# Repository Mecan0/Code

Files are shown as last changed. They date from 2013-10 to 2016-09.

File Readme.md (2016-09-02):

IMPRESORA 3D POWERCODE
 
LISTA DE MATERIALES
 
MARCO COMPLETO POWERCODE CON PLATAFORMA NIVELABLE 3 PUNTOS (7 PIEZAS)

1-. CAJA TORNILLERÍA Y PEQUEÑO MATERIAL:

1 TORNILLERÍA COMPLETA (Ver despiece), 
2 POLEAS GT2 20 DIENTES, 
2 ACOPLADORES 5X5, 
11 RODAMIENTOS LINEALES LM8UU 2 METÁLICOS Y 9 PLÁSTICOS, 
4 PINZAS PARA CRISTAL, 
2 RODAMIENTOS 685ZZ, 
20 BRIDAS 2.5 X 100, 4 BRIDAS 3.5X150,
2 CORREAS GT2 (850 mm Eje X y 650 mm Eje Y)

2-. PAQUETE PLATAFORMA CALIENTE

PLATAFORMA CALIENTE
1 CRISTAL (Ver plano)
1 LÁMINA DE CORCHO 215 X 215 y trozo.
1 CABLE ROJO-NEGRO, TERMISTOR Y FUNDA TERMORETRÁCTIL.

3-. VARILLAS LISAS Y ROSCADAS

4 VARILLAS LISAS CALIBRADAS  ACERO F114 CROMADO 8 X 380 MM
2 VARILLAS LISAS CALIBRADAS ACERO F114 CROMADO X 330 MM
2 VARILLAS ROSCADAS M10X390
2 VARILLAS ROSCADAS M5X300

4-. SOPORTE ROLLO

2 VARILLAS M8X180, TUBO GEWIS 20X220, 4 TUERCAS M8 Y ARANDELAS PIEZAS PLÁSTICAS.

5-. EXTRUSOR Y FUSOR

EXTRUSOR TITAN + HOTEND E3D LITE V6 Y CABLEADO.

6-. MOTORES:

5 MOTORES PASO A PASO MOTECH, 200 PASOS/REV, 4500 KG· CM, CON CONECTOR Y EJE FRESADO, 40 MM DE LONGITUD. REF: MT1703HS168A  160118.
5 CABLES PARA MOTORES. 

7-. FUENTE DE ALIMENTACIÓN

1 FUENTE DE ALIMENTACIÓN 12v 20A, 

8-. CABLEADO POTENCIA Y CONEXIÓN USB.

1  CABLE ALIMENTACIÓN 230V CON ENCHUFE  SCHUCO 1M,
1 CABLE USB  1.8M, 
1 CABLE ALIMENTACIÓN ELECTRÓNICA 12V, 4x1MM DE 53 CM.
1 INTERUPTOR

9-. ELECTRÓNICA

1 ELECTRÓNICA RAMPS 1.4SB
1 ARDUINO MEGA 2560 R3,
 4 DRIVERS DRV8825 (32 MICROPASOS) con DISIPADORES Y FIRMWARE CARGADO.  

10-. DISPLAY, BLOWER Y FINALES DE CARRERA

1 DISPLAY LCD 20X4
1 VENTILADOR RADIAL 50X50X15 12v (BLOWER) Y 1 CABLE PARA BLOWER 60 CM,
3 FINALES DE CARRERA PCB CON CONECTOR Y CABLE DE 70 CM.

11-.  TORNILLERÍA POWER CODE 3P EXTRUSOR E3D+TITAN

16	Torn 3x10 para plástico	 		Para finales de carrera 9, ventilador 3, Xend 2
12	M3x10	 DIN912		Para motores  2+2+2+3, para fuente 2.
10	M3x16	 DIN912		Para plataforma 4, LCD 4,
5	M3x20	 DIN912		Para ventilador 2
10	M3x25	 DIN912		Para electrónica 3, Para LCD 2,
 		 		
30	Tuercas M3	DIN934		
30	Arandelas M3	DIN125		
 		 		
2	Tornillo M5x25 	DIN933		Para tensores 2
1	Tornillo M5x40	DIN84		Para tensor X
2	Varillas M5x300	 		
 		 		
6	Tuercas M5	DIN934		Para eje Z 2, para tensores 3,
2	Tuercas M5 autoblocantes	DIN985		Para tensores 2
10	Arandelas M5	DIN125		Para tensores 4x2
8	Arandelas M5 vuelo	DIN9021		Para tensores 3x2
 		 		
13	Tornillos Seta M6x20	DIN603		Para Marco 4, para diagonales 8, motor Y 1,
2	Tornillos M6x30	DIN84		Para plataforma abajo 1 y Para tensor Y 1
1	Tornilo de M6x35	DIN933		Para plataforma rótula 1
2	Esparragos M6 	 		Para nivelado plataforma
 		 		
30	Tuercas M6	DIN934		
2	Tuercas M6 autoblocantes	DIN985		Para Plataforma nivelable
20	Arandelas M6	DIN125		
10	Arandelas M6 vuelo	DIN9021		
 		 		
2	Varillas M10x390	 		Eje Y
12	Tuercas M10	DIN934		Para varillas 12
8	Arandelas M10	DIN125		Para varillas 8
4	Arandelas M10 Vuelo	DIN9021		Para varillas con marco 4

Para soporte rollo	 		
 		 		
2	Varillas M8x180	 		
4	Tuercas M8	 		
2	Arandelas M8	 		
1	Tubo Gewis de 20x220mm	 		

Basada en la Prusa I3. Xcarriage basado en el diseño de Girobot, soporte del LCD basado en Prusa Hephestos de BQ.

Licencia creative commons, attribution, share alike.

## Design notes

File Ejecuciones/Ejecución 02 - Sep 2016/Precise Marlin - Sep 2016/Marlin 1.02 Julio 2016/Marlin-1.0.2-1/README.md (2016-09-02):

# Marlin 3D Printer Firmware


 Documentation has moved to [marlinfirmware.org](http://www.marlinfirmware.org).

## Release Branch

The Release branch contains the latest tagged version of Marlin (currently 1.0.2 – January 2015). It also includes a version 1.0.1 (December 2014). Any version of Marlin before 1.0.1 (when we started tagging versions) can be collectively referred to as Marlin 1.0.0.

For the most up-to-date Marlin code, please go to the [Development branch](https://github.com/MarlinFirmware/Marlin/tree/Development) – __Not for production use – use with caution!__ When reporting any issues, please check to see if they are resolved in the Development branch first. But let us know if issues exist in tagged releases so we may document and patch them.

## Current Status: In Development

Marlin development is being accelerated to catch up with a long list of issues. Check the Issues and Pull Requests links on the right to to see what we are currently working on.




##### [RepRap.org Wiki Page](http://reprap.org/wiki/Marlin)

## Contact

__Google Hangout:__ <a href="https://plus.google.com/hangouts/_/gxn3wrea5gdhoo223yimsiforia" target="_blank">. Hangout</a> We have a hangout every 2 weeks. Search the issue list for "Hangout" and you will see what time and date the next event is going on.

## Credits

The current Marlin dev team consists of:

 - Scott Lahteine [@thinkyhead] - English
 - Andreas Hardtung [@AnHardt] - Deutsch, English
 - [@Wurstnase] - Deutsch, English
 - [@fmalpartida] - English, Spanish
 - [@CONSULitAS] - Deutsch, English
 - [@maverikou]
 - Chris Palmer [@nophead]
 - [@paclema]
 - [@epatel]
 - Erik van der Zalm [@ErikZalm]
 - David Braam [@daid]
 - Bernhard Kubicek [@bkubicek]

More features have been added by:
  - Lampmaker,
  - Bradley Feldman,
  - and others...

## License

Marlin is published under the [GPL license](/Documentation/COPYING.md) because We believe in open development.
Do not use this code in products (3D printers, CNC etc) that are closed source or are crippled by a patent.



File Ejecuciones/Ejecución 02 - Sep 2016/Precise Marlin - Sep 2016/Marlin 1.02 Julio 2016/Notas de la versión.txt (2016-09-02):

Basado en Marlin 1.02-1

Cambio el autor de la modificación y la fecha de modificación

Elegir la electrónica:

#define MOTHERBOARD BOARD_RAMPS_13_EFB

Descomentamos la siguiente línea y le damos un nombre:

#define CUSTOM_MENDEL_NAME "PowerCode"

Elegimos los termistores colocados

#define TEMP_SENSOR_0 5
#define TEMP_SENSOR_1 0
#define TEMP_SENSOR_2 0
#define TEMP_SENSOR_BED 1

Limito la temperatura del extrusor principal a 250º

#define HEATER_0_MAXTEMP 250

Seguidamente editamos el PID

// PowerCode con E3D V6 Lite, Thermistor 5, Resistencia 12V a 30W cable azul
// La ultima medició ha sido con en Verano con 30 º

    #define  DEFAULT_Kp 49 //41 // 45.30
    #define  DEFAULT_Ki 7 //5.50 // 6.50
    #define  DEFAULT_Kd 83 //75 // 80.30

Invertimos la dirección del extrusor

#define INVERT_E0_DIR true   // Titan 

Definimos los limites de la impresora

#define X_MAX_POS 195
#define X_MIN_POS 0
#define Y_MAX_POS 190
#define Y_MIN_POS 0
#define Z_MAX_POS 180
#define Z_MIN_POS 0

Colocamos aceleraciones y pasos por mm

//// MOVEMENT SETTINGS
#define NUM_AXIS 4 // The axis order in all axis related arrays is X, Y, Z, E
#define HOMING_FEEDRATE {35*60, 35*60, 2,5*60, 0} //{50*60, 50*60, 4*60, 0}  // set the homing speeds (mm/min)

// default settings

#define DEFAULT_AXIS_STEPS_PER_UNIT   {160.9, 160.9, 8000, 912}  // Driver DRV8825 con 32 micropasos
#define DEFAULT_MAX_FEEDRATE          {200, 200, 2.5, 15} // {500, 500, 5, 25}  // (mm/sec)
#define DEFAULT_MAX_ACCELERATION      {500,500,50,1000} //{9000,9000,100,10000}    // X, Y, Z, E maximum start speed for accelerated moves. E default values are good for Skeinforge 40+, for older versions raise them a lot.

#define DEFAULT_ACCELERATION          500 //3000    // X, Y, Z and E max acceleration in mm/s^2 for printing moves
#define DEFAULT_RETRACT_ACCELERATION  1000 //3000  // X, Y, Z and E max acceleration in mm/s^2 for retracts

Y el Jerk

#define DEFAULT_XYJERK                10.0    // (mm/sec)

Finalmente activamos el LCD

#define REPRAP_DISCOUNT_SMART_CONTROLLER

///////////////////////////////////////////////////////////////////

En la pestaña Language.h elegimos el Español:

#define LANGUAGE_INCLUDE GENERATE_LANGUAGE_INCLUDE(es)

///////////////////////////////////////////////////////////////////

En la ventana configuration_adv, cambiar el retroceso del final de carrera Z a 1

#define Z_HOME_RETRACT_MM 1

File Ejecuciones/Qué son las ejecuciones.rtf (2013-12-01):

¿Qué son las ejecuciones?
Una ejecución es una forma completamente definida de construir la PowerCode, es decir definiendo los rodamientos lineales, el extrusor y hot-end , la electrónica utilizada… todo. De esta forma podremos tener documentación más precisa y completa para cada forma de construir una Code.

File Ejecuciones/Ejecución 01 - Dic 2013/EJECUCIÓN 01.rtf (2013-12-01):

EJECUCIÓN 01

Rodamientos lineales Igus
Electrónica RAMPS
Extrusor tipo Greg Extruder
Hot-end E3D

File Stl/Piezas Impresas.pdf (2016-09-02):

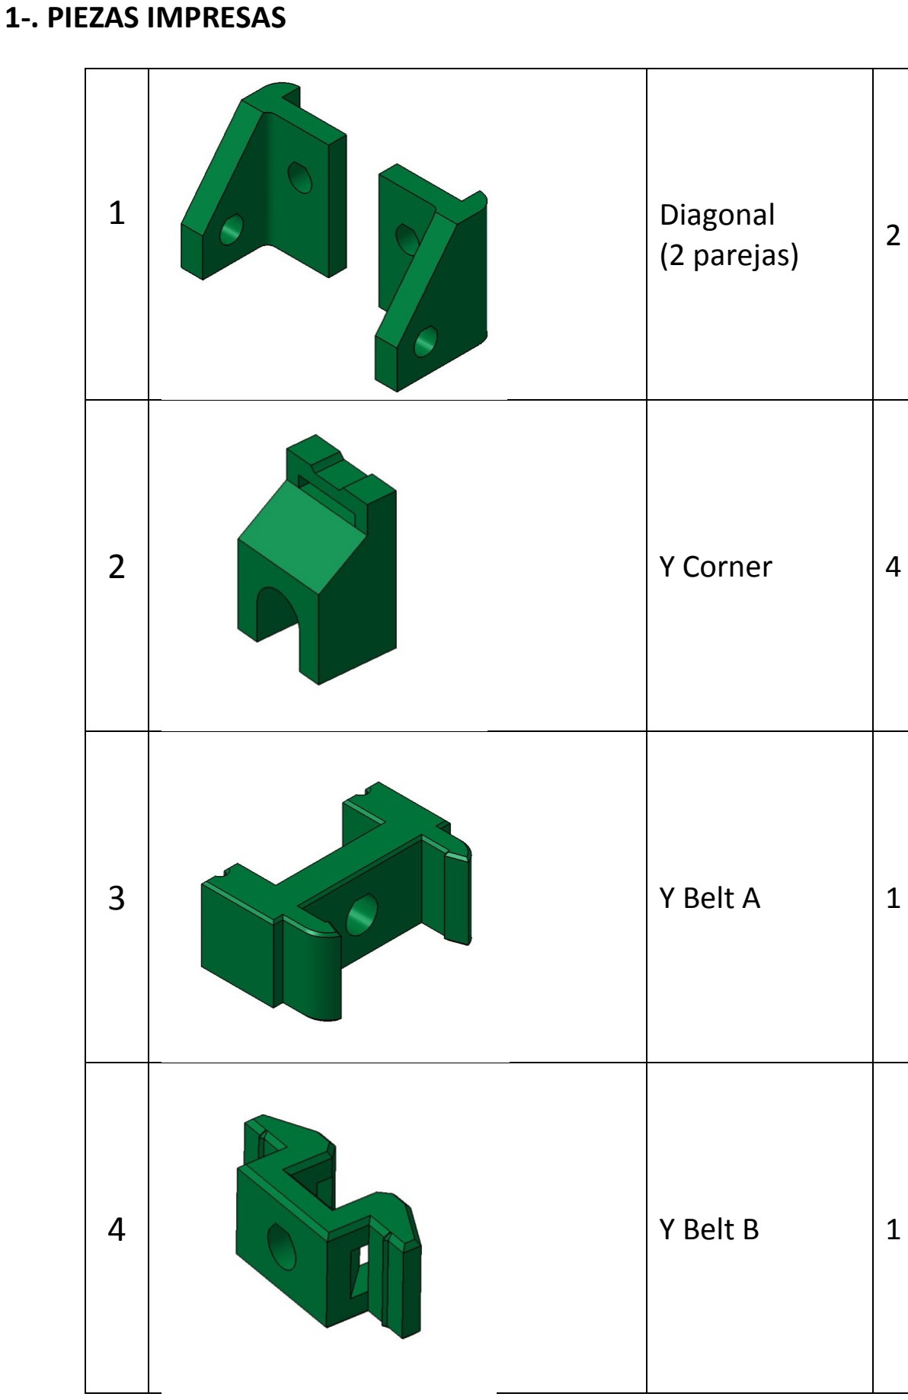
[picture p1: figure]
1-. PIEZAS IMPRESAS; Diagonal (2 parejas); Y Corner; Y Belt A; Y Belt B

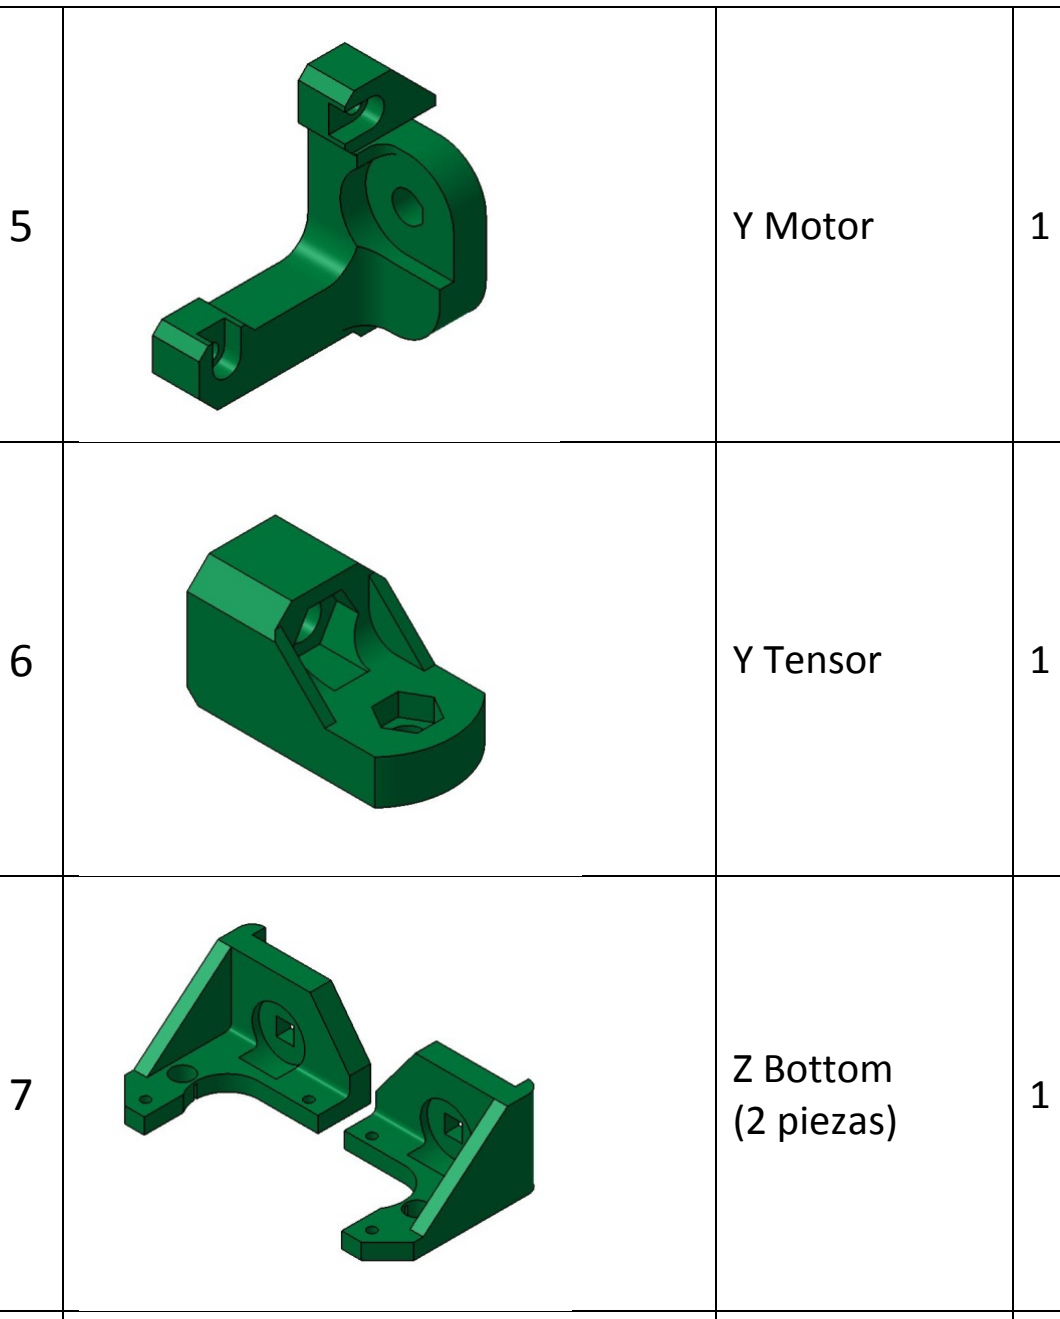
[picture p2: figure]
Y Motor; Y Tensor; Z Bottom (2 piezas)
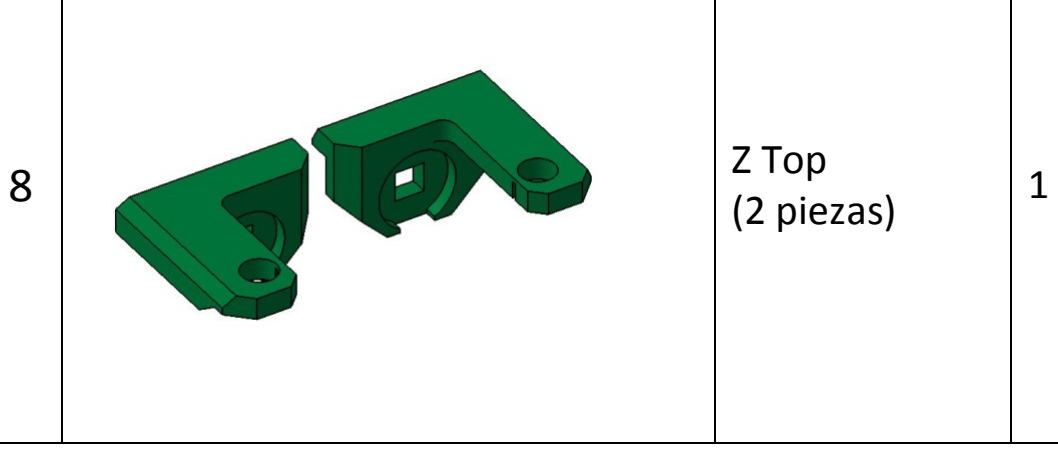
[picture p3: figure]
Z Top (2 piezas)

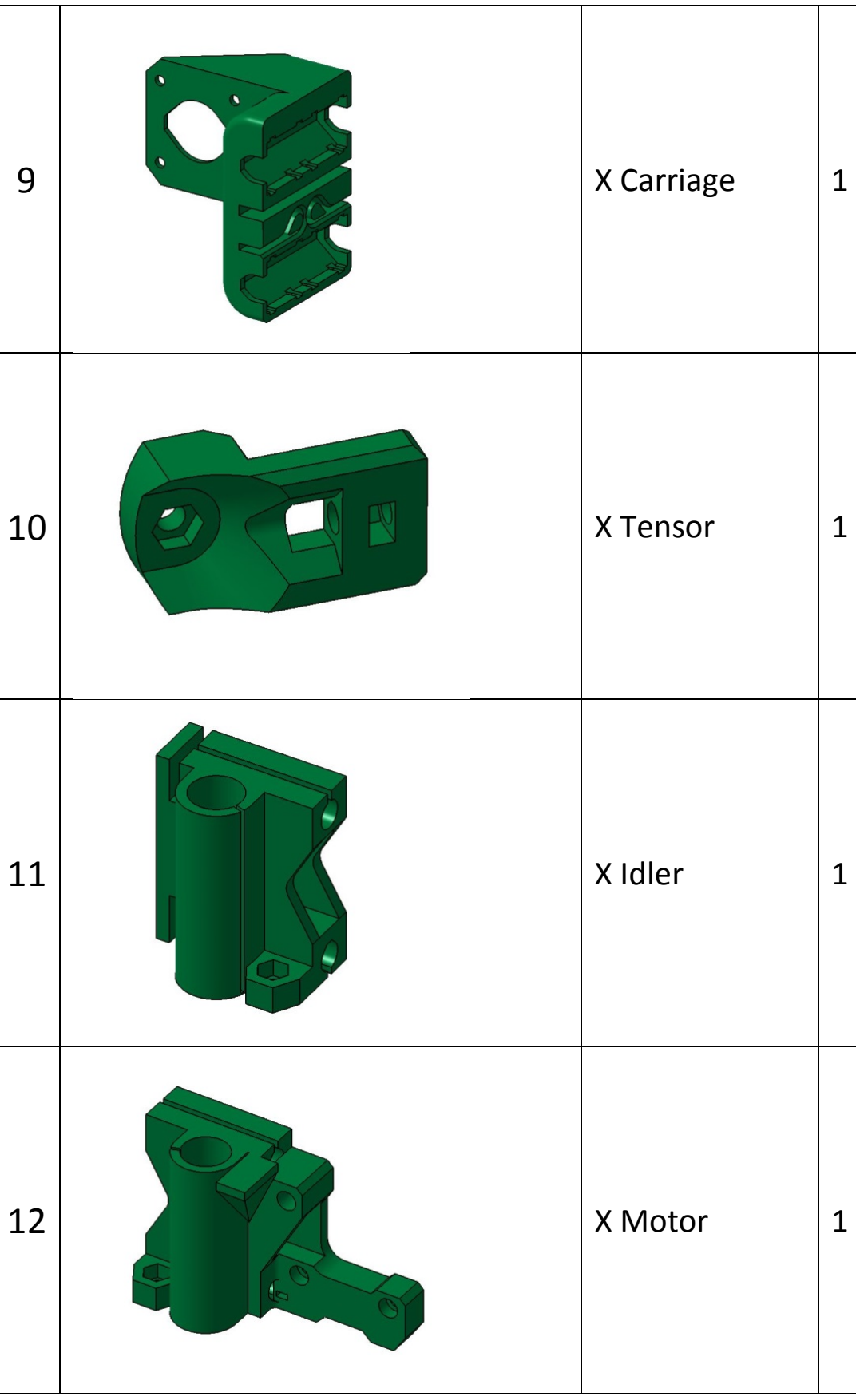
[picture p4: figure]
X Carriage; X Tensor; X Idler; X Motor

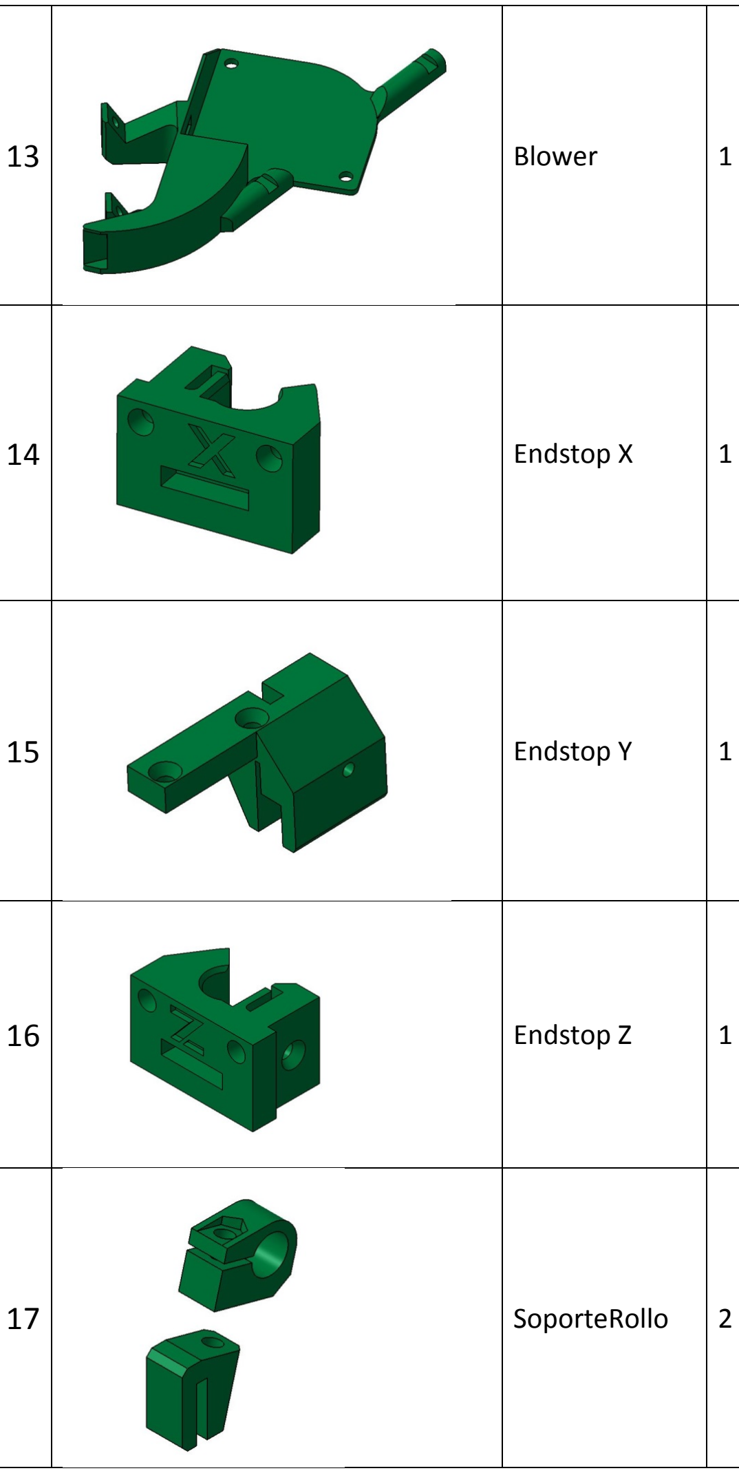
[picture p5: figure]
Blower; Endstop X; Endstop Y; Endstop Z; SoporteRollo

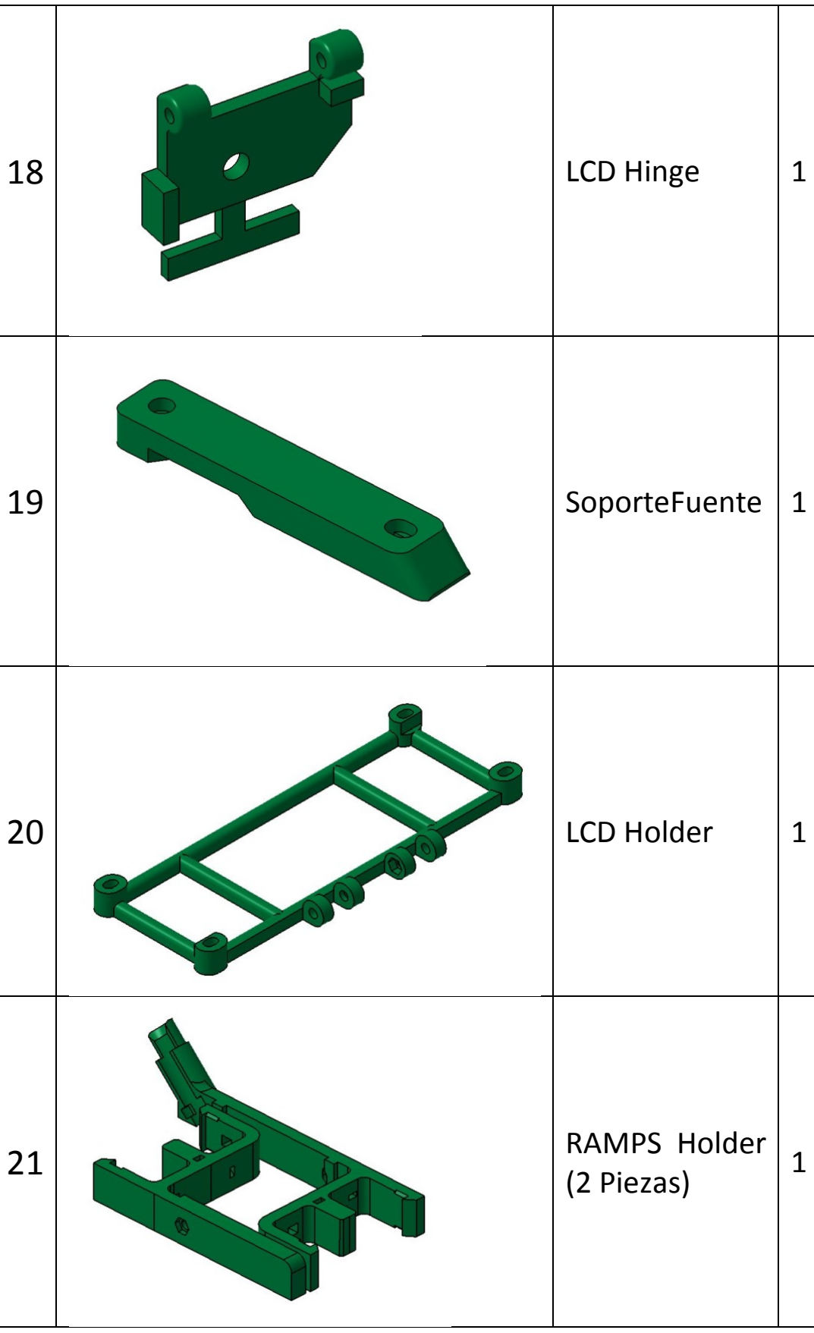
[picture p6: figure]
LCD Hinge; SoporteFuente; LCD Holder; RAMPS Holder (2 Piezas)

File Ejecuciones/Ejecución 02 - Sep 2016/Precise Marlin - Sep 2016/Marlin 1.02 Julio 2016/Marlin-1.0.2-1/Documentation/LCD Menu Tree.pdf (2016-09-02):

# Marlin LCD Menu Tree

Main Menu | Tune Menu | Move Menu
Info screen | Main | Prepare
Tune | Speed | Move 10mm | Move Menu
Prepare | Nozzle | Move 1mm | Move axis
Control | Nozzle2 | Move 0.1mm | Move X
Pause print | Nozzle3 | | Move Y
Resume print | Bed | | Move Z
Stop print | Fan speed | Temperature Menu | Extruder
Print from SD | Flow | Control
Change SD card | Babystep X | Nozzle
No SD card | Babystep Y | Nozzle2
Init. SD card | Babystep Z | Nozzle3
| Change filament | Bed
| | Fan speed
| | Autotemp
| Prepare Menu | \002 Min
| Main | \002 Max | Preheat PLA
| Autostart | \002 Fact | Temperature
| Disable steppers | PID-P | Fan speed
| Auto home | PID-I | Nozzle
| Preheat PLA | PID-D | Bed
| Preheat ABS | PID-C | Store memory
| Cooldown | Preheat PLA conf
| Switch power off | Preheat ABS conf | Preheat ABS
Switch power on | Temperature
Move axis | Fan speed
| Motion Menu | Nozzle
| Control | Bed
Control Menu | Z Offset | Store memory
Main | Accel
Temperature | Vxy-jerk
Motion | Vz-jerk
LCD contrast | Ve-jerk
Retract | Vmax x
Store memory | Vmax y
Load memory | Vmax z
Restore failsafe | Vmax e
| Vmin
| VTrav min
SD Card Menu | Amax x
Main | Amax y
Refresh | Amax z
filenames | Amax e
| A-retract
| Xsteps/mm
| Ysteps/mm
| Zsteps/mm
| Esteps/mm
| Endstop abort

Retract Menu
Control
AutoRetr.
Retract mm
Retract F
Hop mm
UnRet +mm
UnRet F

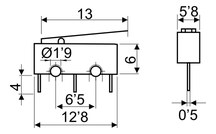
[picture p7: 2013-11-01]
Fuentes/Code Endstop Holder/FinaldeCarrera.png

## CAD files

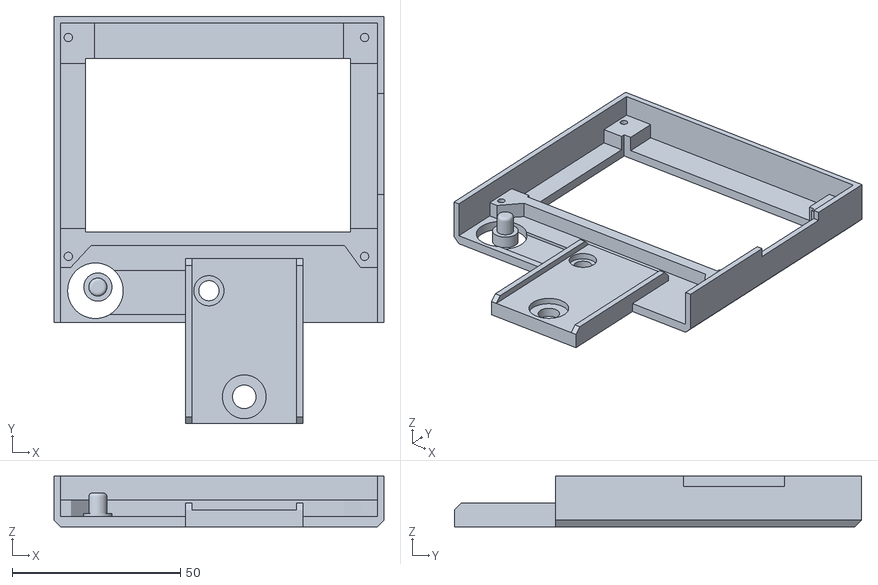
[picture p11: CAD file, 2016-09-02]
Stl/20 LCD FullGraphics.stl
98.0 x 121.0 x 15.0

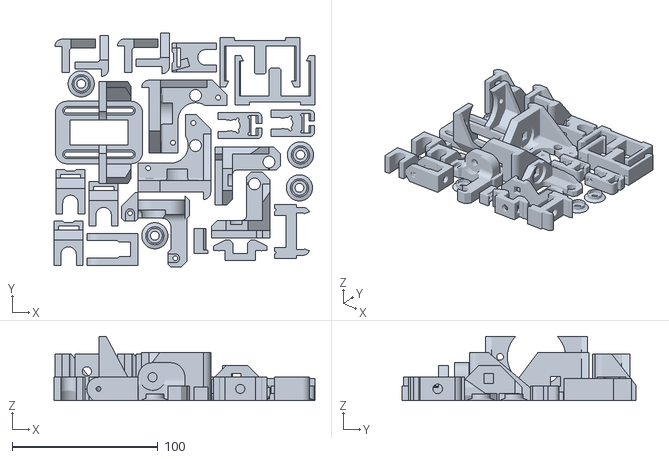
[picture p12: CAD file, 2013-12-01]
Ejecuciones/Ejecución 01 - Dic 2013/Code_Plato_1.stl
179.2 x 160.7 x 44.0

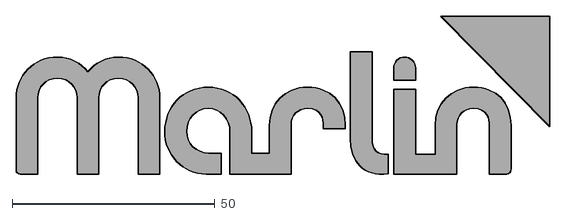
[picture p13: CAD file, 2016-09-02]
Ejecuciones/Ejecución 02 - Sep 2016/Precise Marlin - Sep 2016/Marlin 1.02 Julio 2016/Marlin-1.0.2-1/Documentation/Logo/Marlin Logo.dxf
131.6 x 39.5

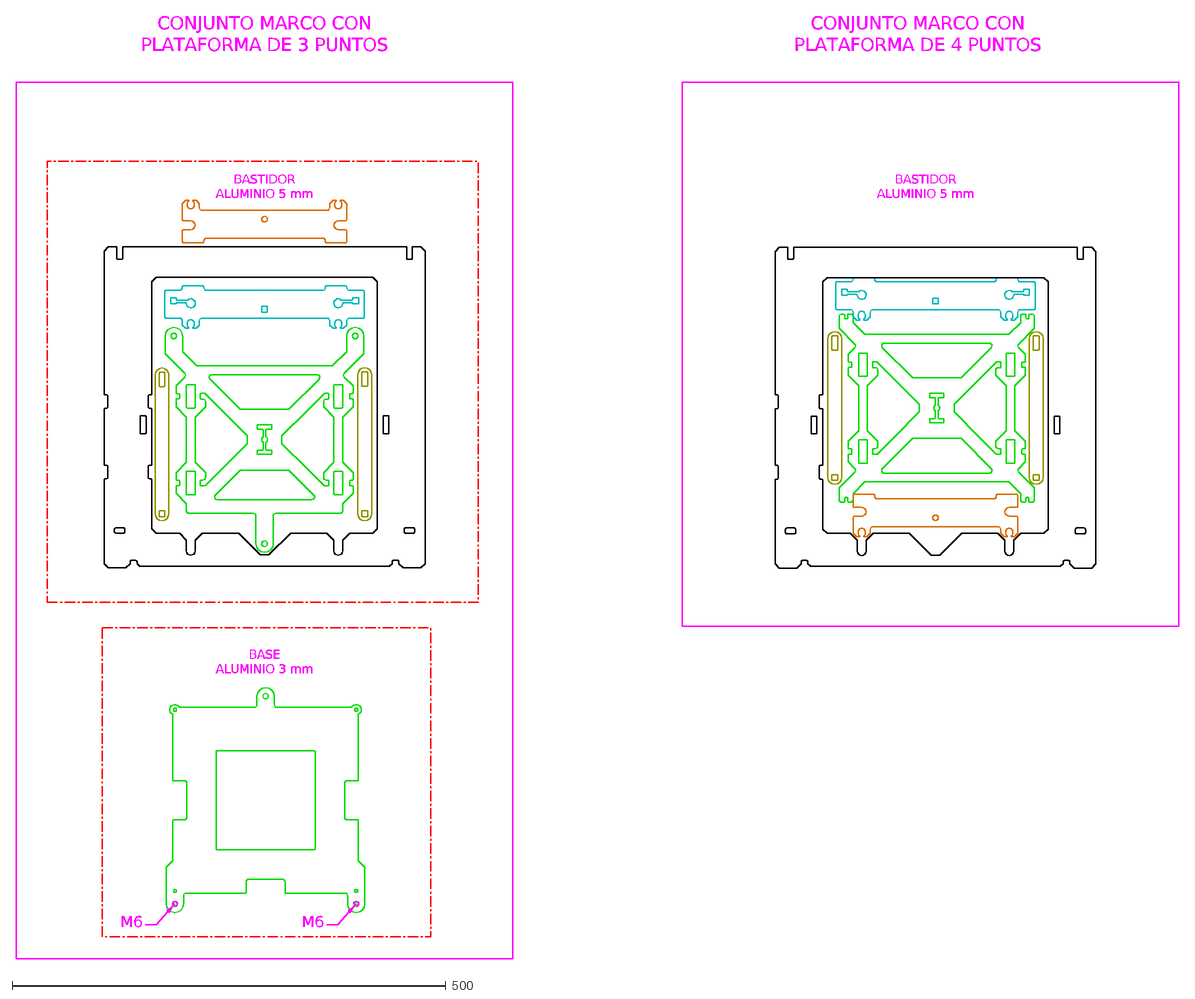
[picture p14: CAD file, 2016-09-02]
Fuentes/Code Aluminio/Aluminio Power Code.dxf
CONJUNTO MARCO CON PLATAFORMA DE 3 PUNTOS
BASE ALUMINIO 3 mm
BASTIDOR ALUMINIO 5 mm
CONJUNTO MARCO CON PLATAFORMA DE 4 PUNTOS
M6

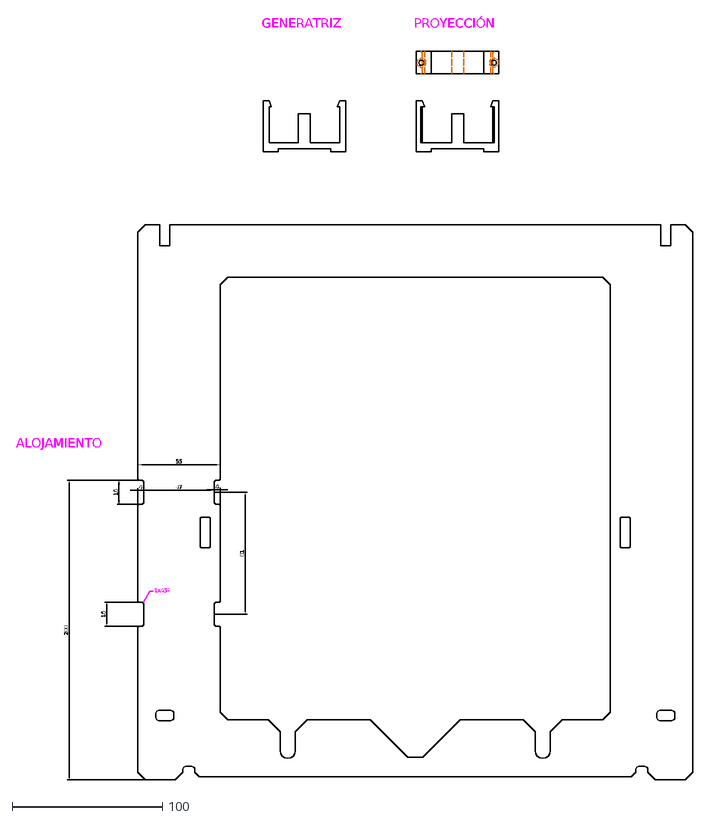
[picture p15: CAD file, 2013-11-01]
Fuentes/Code Clip RAMPS/Code Clip RAMPS.dxf
GENERATRIZ
PROYECCIÓN
16
55
47
4
200
81
1x45º
ALOJAMIENTO

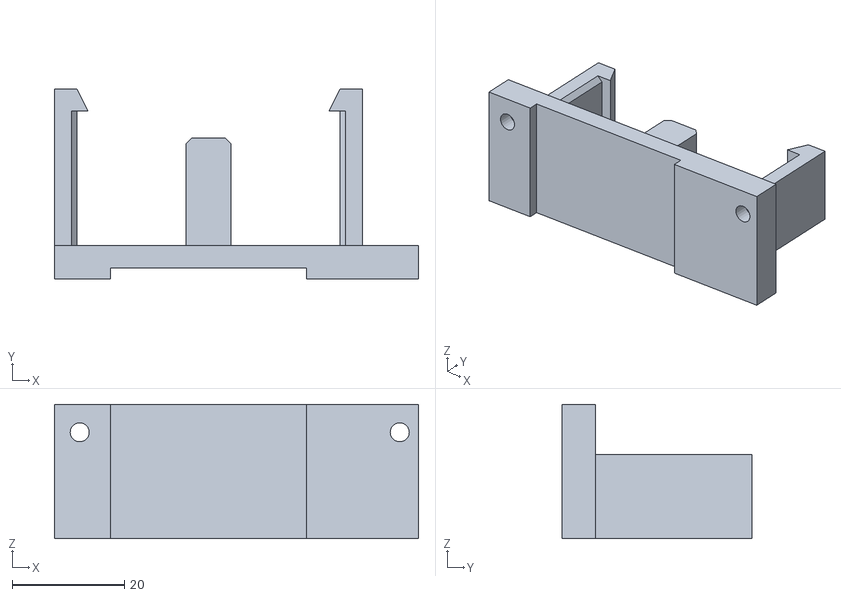
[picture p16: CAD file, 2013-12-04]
Fuentes/Code Clip SAV MK1/Code_Clip_SAV-MK1_arriba.stl
65.0 x 34.0 x 24.0

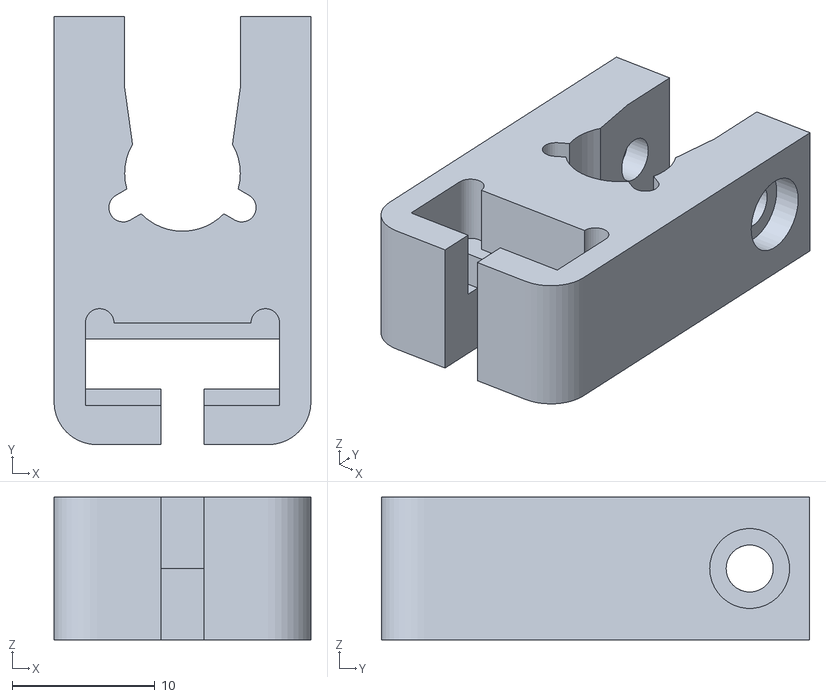
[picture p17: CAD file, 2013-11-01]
Fuentes/Code Endstop Holder/Code_EndStop (x2).stl
18.0 x 30.0 x 10.0

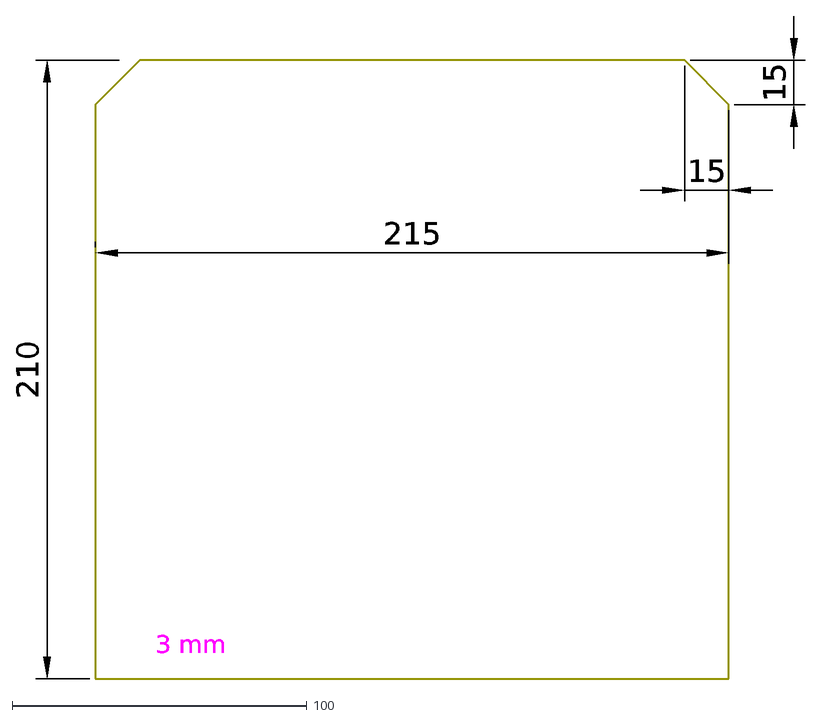
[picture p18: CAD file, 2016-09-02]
Fuentes/Cristal.dxf
215
210
15
3 mm

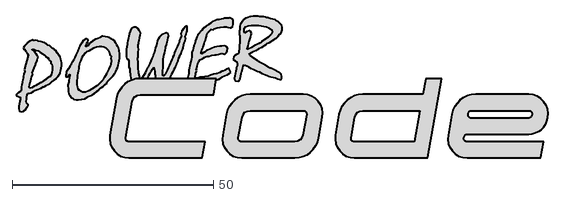
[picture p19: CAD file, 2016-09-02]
Logos/LogoPowerCode.dxf
132.3 x 35.2

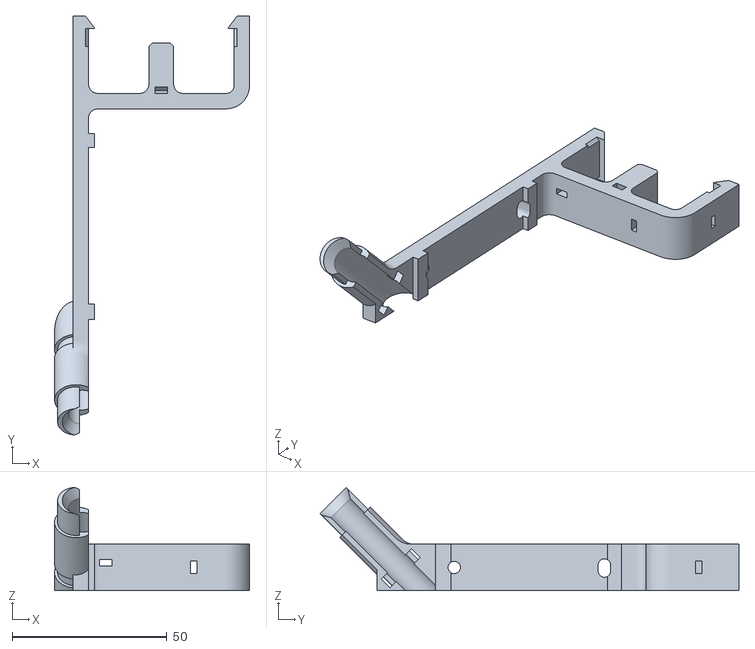
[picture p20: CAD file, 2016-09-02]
Stl/21 RampsHolder Abajo.stl
63.0 x 135.4 x 33.4

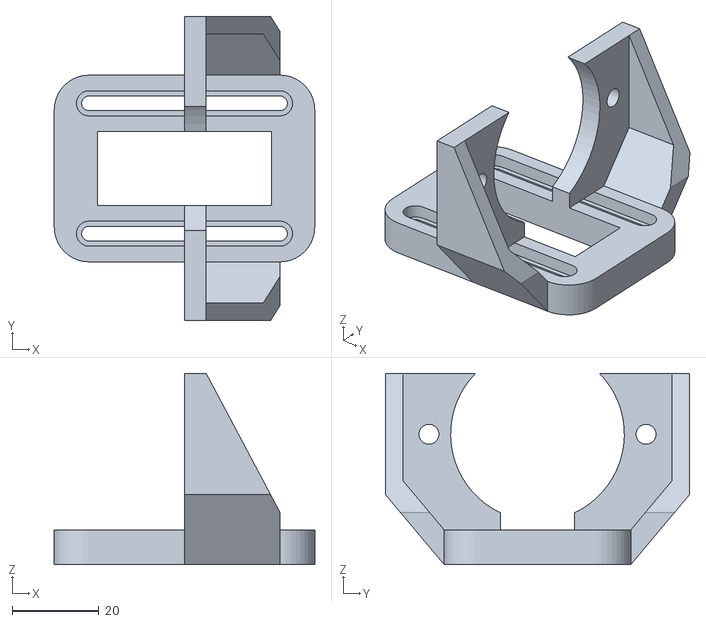
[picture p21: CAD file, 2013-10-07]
Stl/Extruder/Code_LevelExtruder.stl
60.0 x 70.0 x 44.0

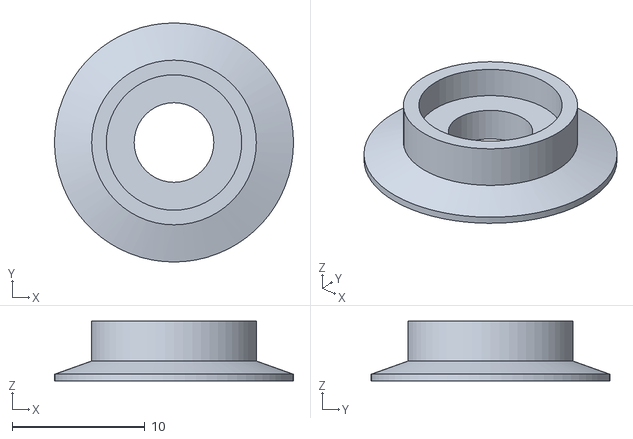
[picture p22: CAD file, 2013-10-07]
Stl/Opcionales-Experimentales/Code_Pulley_623 (x4) diam 10.2.stl
18.0 x 18.0 x 4.50

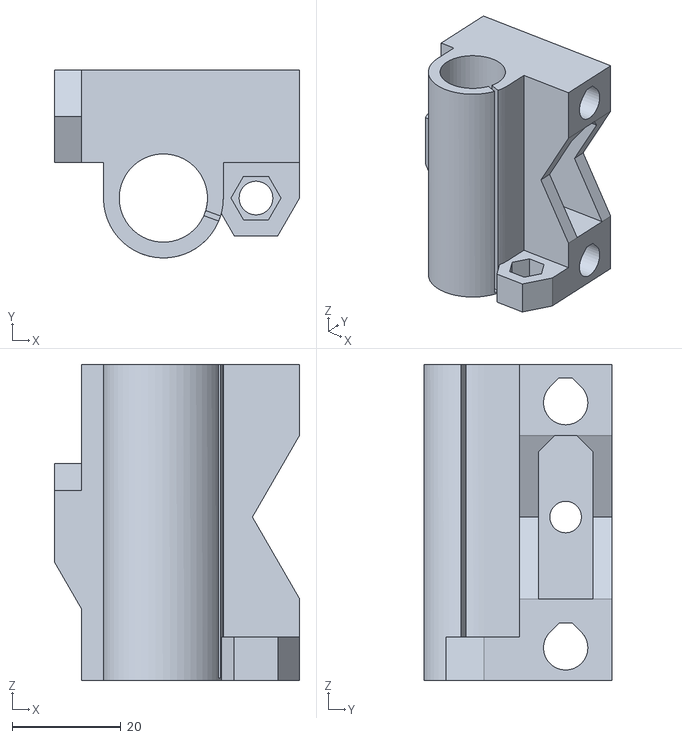
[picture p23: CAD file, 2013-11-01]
Stl/Para Igus/Code_Xend_Idler_A_Igus.stl
45.0 x 34.5 x 58.0

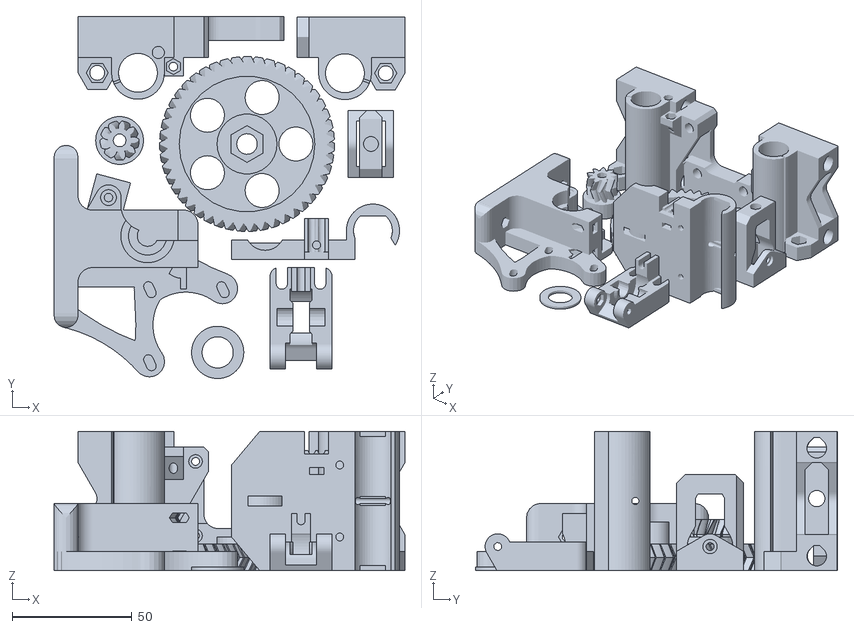
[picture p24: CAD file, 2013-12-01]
Ejecuciones/Ejecución 01 - Dic 2013/Code_Plato_2.stl
146.3 x 151.0 x 58.0

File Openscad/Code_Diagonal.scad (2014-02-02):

// Created from Code_Diagonal (x2).stl
// https://github.com/Mecan0/Code
// By J.Rodigo (www.jra.so)
// Licence Creative commons atribution & share alike.

/**************************/
// Parámetros de la pieza  /
/**************************/

dTalaX = 6.4;	//Diámetro del taladro del bloque X 

dTalaY = 6.4;	//Diámetro del taladro del bloque Y 


// Bloque a lo largo del eje X
module bloqueX(){
	// Bloque y taladro
	difference () {
		translate([0, -6, 0])
		cube([23, 6, 32]);
	
		translate([14.67, 1, 8])
		rotate( 90, [1, 0, 0])
		cylinder(h = 8, r = dTalaX/2, $fn=100);
	}

	// Esquina redondeada
	difference () {
		translate([0, -5, 0])
		cylinder(h = 32, r = 5, $fn=100);

		translate([-5, -10, -1])
		cube([10, 5, 34]);
	}	
}

// Bloque a lo largo del eje Y
module bloqueY(){
	// Bloque y taladro
	difference () {
		translate([0, -23, 0])
		cube([5, 23, 32]);

		translate([-1, -14.66, 20])
		rotate( 90, [0, 1, 0])
		cylinder(h = 7, r = dTalaY/2, $fn=100);
	}
}

// Redondeo entre los bloques X y Y
module redondeoXY(){
	difference () {
		cube([2, 2, 32]);
		
		translate([2, 0, -1])
		cylinder(h = 34, r = 2, $fn=100);
	}
}

// Unión de todos los bloques
module pieza(){
	difference () {
		union() {
			bloqueX();

			bloqueY();

			translate([5, -8, 0])
			redondeoXY();
		}	

		//Chaflan que afecta al bloqueX() y al redondeoXY()
		translate([23, -7, 10.55])
		rotate( 38, [0, -1, 0])
		cube([18, 8, 34]);	
	}
}

/**************************/
//  Generamos las piezas   /
/**************************/

// Pieza normal
translate([0, 30, 0])
pieza();

// Pieza simetrica
translate([0, -30, 0])
mirror([ 0, 1, 0 ]) 
pieza();

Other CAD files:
Fuentes/Code Clip SAV MK1/Code_Clip_SAV-MK1.stl
Fuentes/Code Endstop Holder/CodeEndStopHolder.dxf
Logos/LogoCodeNegativo.stl
Stl/09 X_Carriage Titan.stl
Openscad/Code_Config.scad
Openscad/Code_Xend_Motor.scad
Openscad/Code_Ymotor.scad
Fuentes/Code Clip SAV MK1/Code Clip SAVMK1.dxf
Logos/LogoCode.stl
Openscad/Code_Clip_RAMPS.scad
Openscad/Code_Diagonal (x2).scad
Openscad/Code_EndStop.scad
Openscad/Code_LevelExtruder.scad
Openscad/Code_Pulley_623.scad
Openscad/Code_Xcarriage_A (Nuevo).scad
Openscad/Code_Xcarriage_B.scad
Openscad/Code_Xend_Idler_A_M6.scad
Openscad/Code_Xend_Idler_B_623_M6.scad
Openscad/Code_Ybelt_holderA.scad
Openscad/Code_Ybelt_holderB.scad
Openscad/Code_Ycorner.scad
Openscad/Code_Ycorner_Endstop.scad
Openscad/Code_Yidler_623.scad
Openscad/Code_Zbotton.scad
Openscad/Code_Ztop.scad
Stl/01 Diagonal.stl
Stl/02 Ycorner.stl
Stl/03 Ybelt_A.stl
Stl/04 Ybelt_B.stl
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

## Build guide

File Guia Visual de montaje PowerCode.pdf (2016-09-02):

Guía visual de montaje.


SEP-2016

MARCO, PIEZAS METÁLICAS

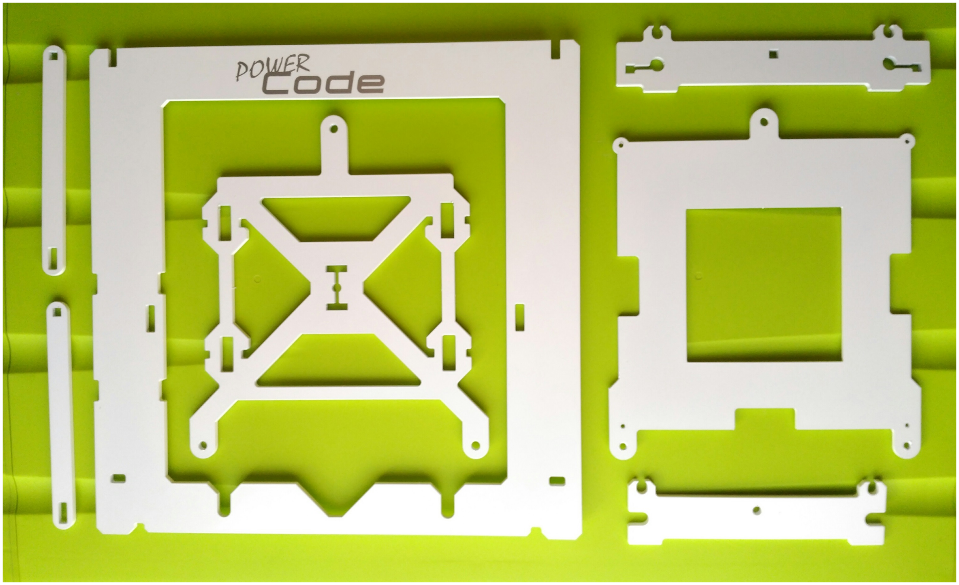
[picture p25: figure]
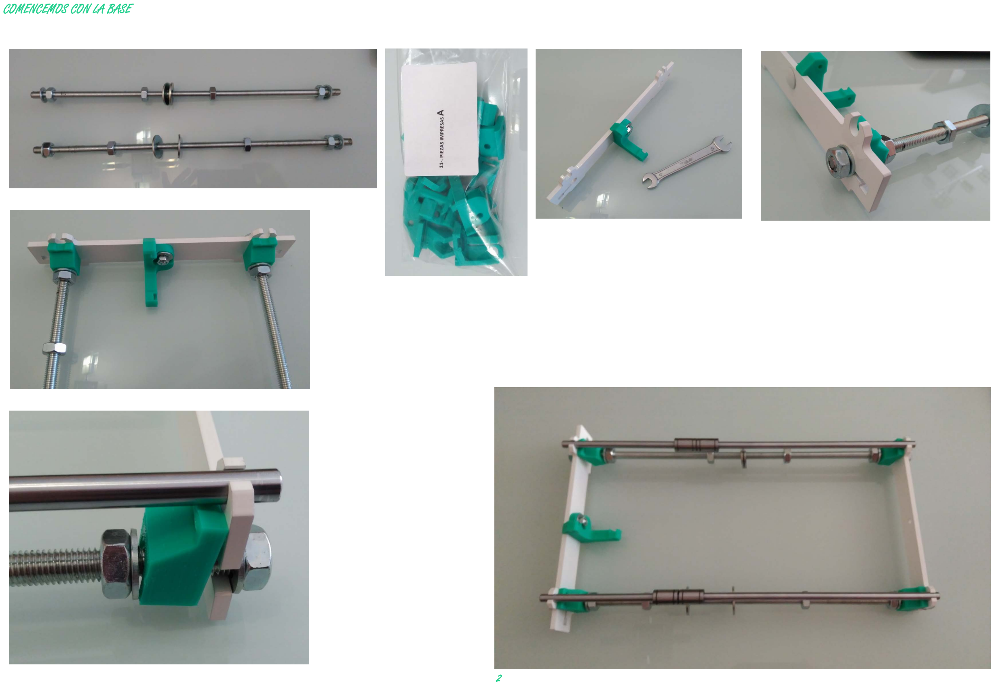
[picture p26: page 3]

COMENCEMOS CON LA BASE

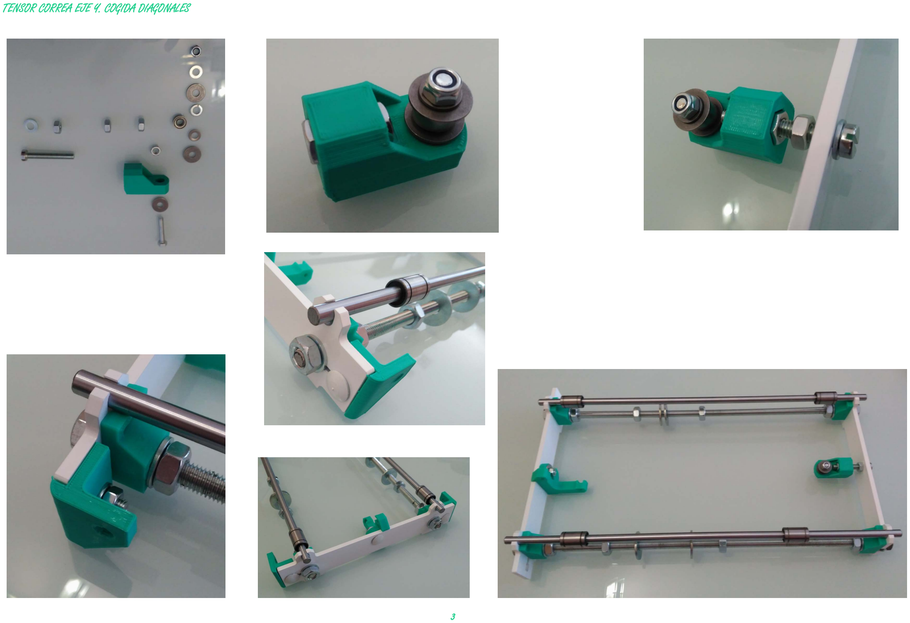
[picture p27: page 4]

TENSOR CORREA EJE Y. COGIDA DIAGONALES

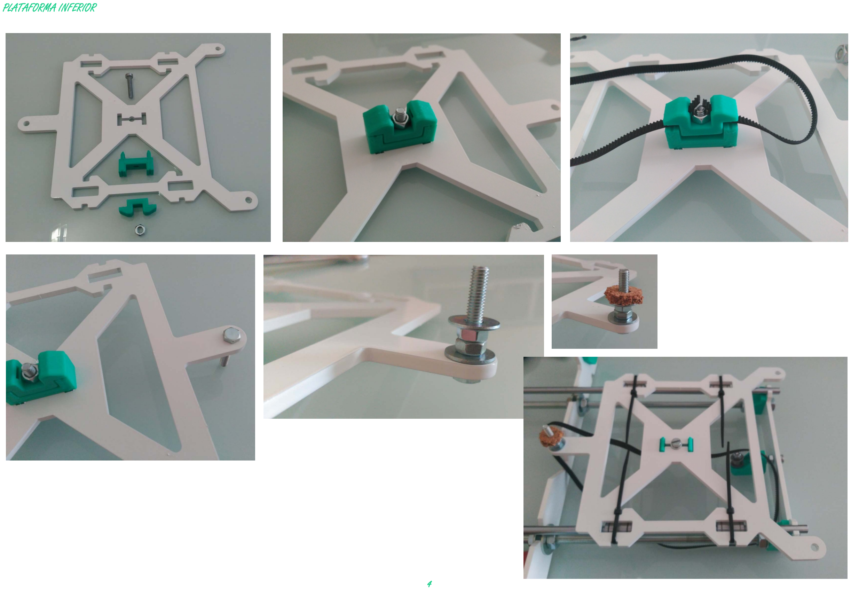
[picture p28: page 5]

PLATAFORMA INFERIOR

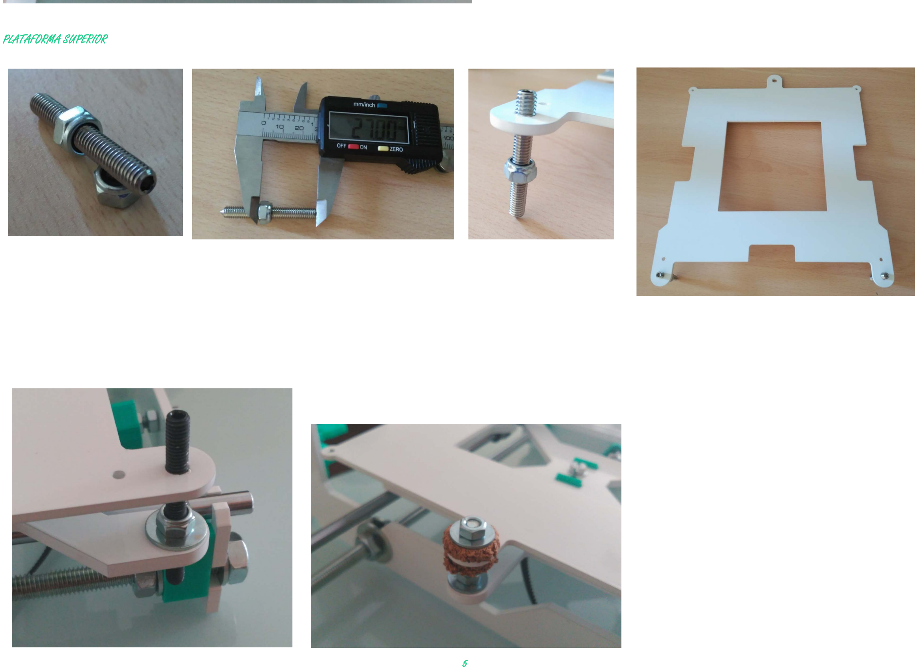
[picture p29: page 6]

PLATAFORMA SUPERIOR

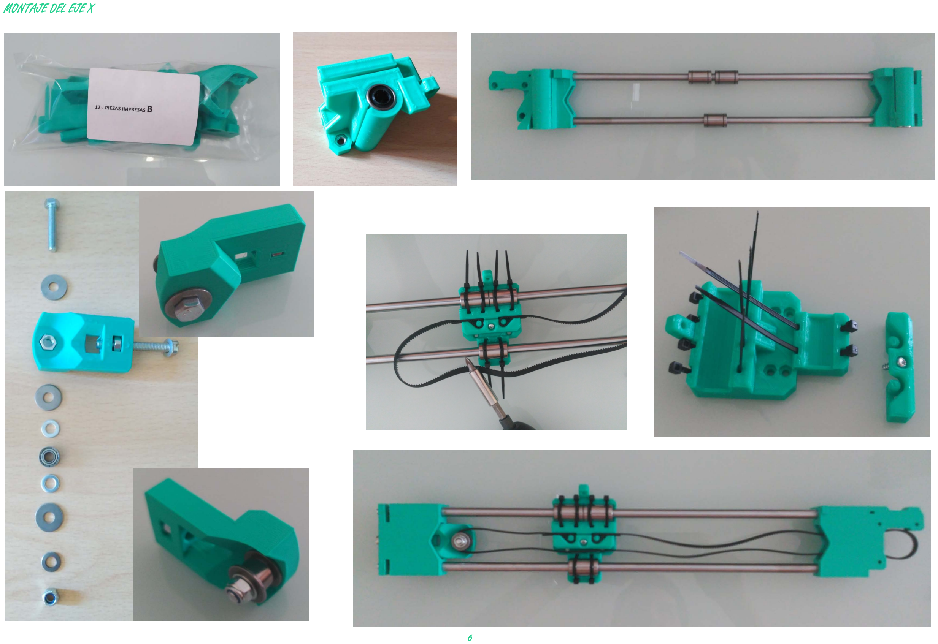
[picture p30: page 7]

MONTAJE DEL EJE X

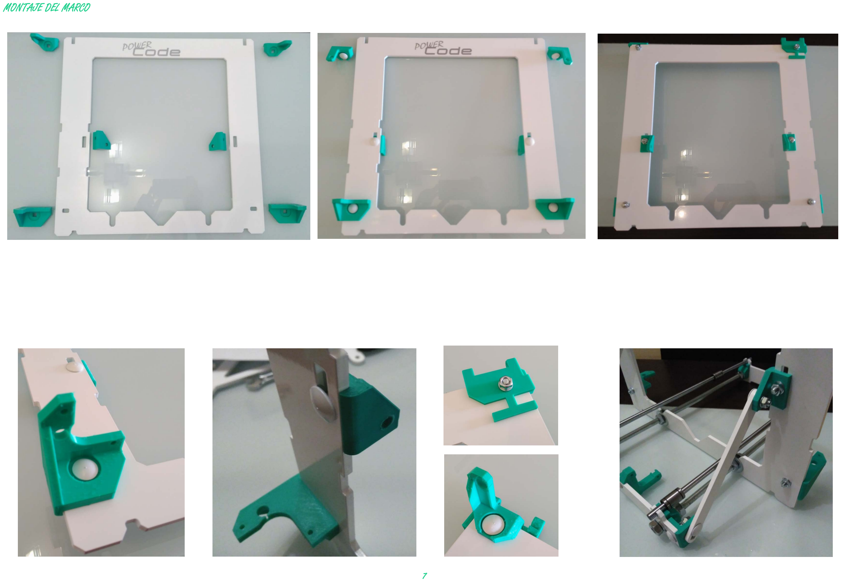
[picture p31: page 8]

MONTAJE DEL MARCO

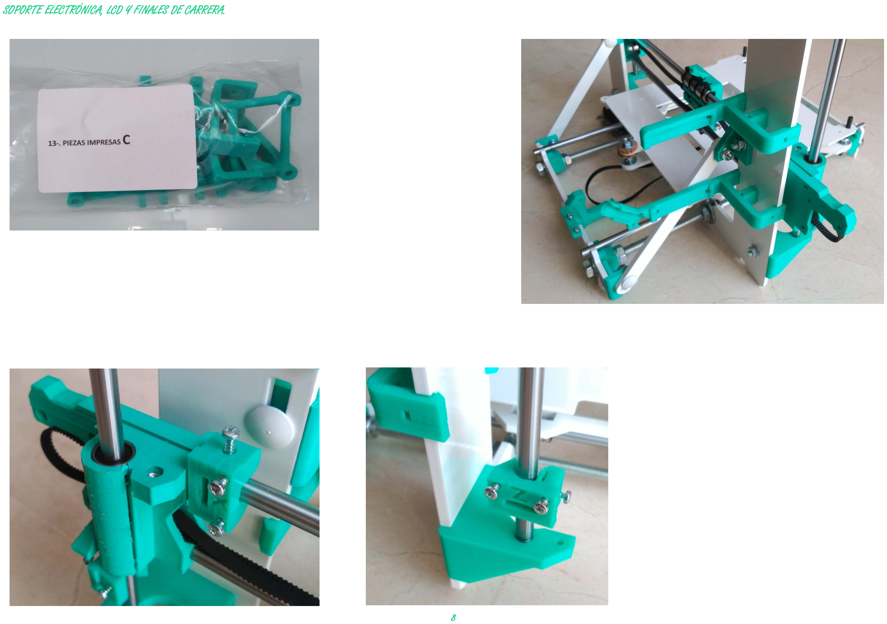
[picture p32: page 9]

SOPORTE ELECTRÓNICA, LCD Y FINALES DE CARRERA.

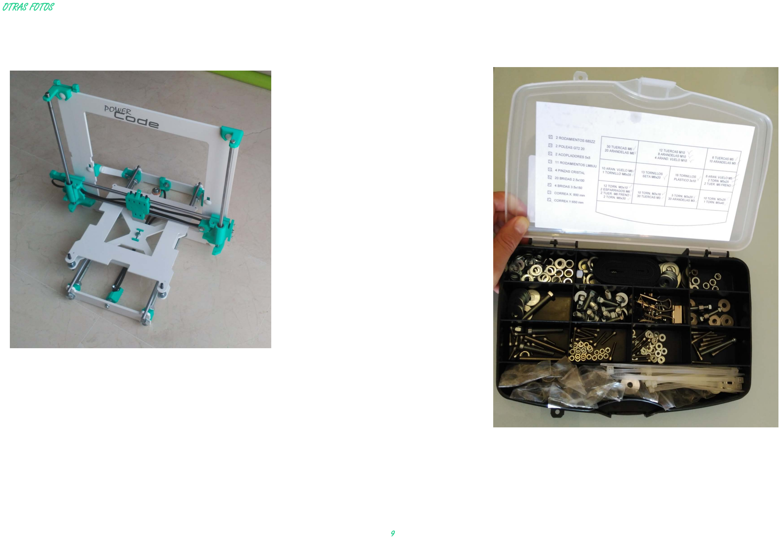
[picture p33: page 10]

OTRAS FOTOS

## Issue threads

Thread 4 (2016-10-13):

Problema con Firmware

DavidAntRuiz, 2016-10-13:
Hola, me gustó mucho su modelo de impresora y decidí llevarlo a cabo, una vez montada y puesta en funcionamiento no consigo configurar el firmware para que imprima, los motores solo hacen ruido y pitidos, no "lleva al origen", he conseguido configurar los finales de carrera pero la impresora se vuelve loca, adjunto mi archivo Configuration.h del Marlin... por favor, ¿Podría echarme una mano? llevo un tiempo dando vuelta a todas las configuraciones y nada... no lo consigo por más vueltas que le doy...

Estoy usando la última versión del Marlin, he intentando cargarle la ultima ejecución que ha subido ud., pero los componentes no son los mismos (Ex, pololus) y tampoco consigo adaptarla...

Los componentes de mi impresora son:

- Ramps 1.4
- LCD full graphic bien configurada pues se ven los menús y demás
- 4 drivers A4988 (calibrados en intensidad)
- NO cama caliente
- 5 Motores comprados en BQ con los colores de los cables según manuales.
- SD de 8GB detectada sin problema
- Estructura 215mmx225mm
- Tres finales de carrera
- Piezas impresas de su archivo de github

Gracias, disculpe las molestias y buen trabajo.

[Configuration.zip](https://github.com/Mecan0/Code/files/527479/Configuration.zip)

Mecan0, 2016-10-14:
Hola, probablemente tengas una versión anticuada de firmware, en
thingiverse coloque una recientemente, si no la localizas o no funciona
házmelo saber.
Últimamente estoy teniendo problemas con ficheros corruptos en github.

M. Palacios

El 13 oct. 2016 5:19 p. m., "DavidAntRuiz" <notifications@github.com>
escribió:

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

DavidAntRuiz, 2016-10-14:
Gracias por responder Manuel.

De acuerdo, lo he encontrado, probaré cuando llegue a casa del trabajo.

Le comento una serie de problemas que me descolocan, por ejemplo, en sus configuraciones en el apartado:

> #define DEFAULT_AXIS_STEPS_PER_UNIT

Yo he tenido que poner los valores  `#define DEFAULT_AXIS_STEPS_PER_UNIT {20,20,200,777}` pero los he puesto de forma aleatoria... ¿Debe llevar una lógica? Pues siempre que veo el valor del eje Z por ejemplo es siempre muy elevado (4000, 8000...) sin embargo, si yo lo pongo con esos valores, el motor solo hace ruido y hace un pitido realmente desagradable, es decir, lo he puesto de manera aleatoria por que ha sido el único valor que ha "funcionado", y cuando digo "funcionado" quiero decir que ha sido la única vez que los ejes se han movido sin golpear con todo lo que había a su paso...

Creo que no estoy haciendo bien absolutamente nada relacionado con los motores... lo único que sé con seguridad que sí funciona son los finales de carrera.

Si me lo permite, adjunto un vídeo para que vea el funcionamiento actual de la impresora, esto ocurre cuando ha terminado de calentar y va a ponerse a imprimir.

Disculpe que se lo envíe todo en `*.ZIP` pero es que el formato de archivos permitidos para compartir es limitado

De todas formas, ya le digo que probaré en cuanto llegue con el que me acabo de descargar de Thingiverse y le comentaré el resultado adjuntando si lo requiere algún vídeo, imagen o archivo.

Saludos.

[Video2016-10-14.zip](https://github.com/Mecan0/Code/files/528928/Video2016-10-14.zip)

Mecan0, 2016-10-14:
Buenas David, ya he podido verlo detenidamente, no sé de donde viene el archivo de Marlin que has usado, cuando metas el que hay en thingiverse funcionará mucho mejor, las varibles de aceleraciones son las siguientes  (que son mas bajas que las que tu tienes):

//// MOVEMENT SETTINGS

#define NUM_AXIS 4 // The axis order in all axis related arrays is X, Y, Z, E

#define HOMING_FEEDRATE {35*60, 35*60, 2,5*60, 0} //{50*60, 50*60, 4*60, 0}  // set the homing speeds (mm/min)

// default settings

#define DEFAULT_AXIS_STEPS_PER_UNIT   {160.9, 160.9, 8000, 912}  // Driver DRV8825 con 32 micropasos

#define DEFAULT_MAX_FEEDRATE          {200, 200, 2.5, 15} // {500, 500, 5, 25}  // (mm/sec)

#define DEFAULT_MAX_ACCELERATION      {500,500,50,1000} //{9000,9000,100,10000}    // X, Y, Z, E maximum start speed for accelerated moves. E default values are good for Skeinforge 40+, for older versions raise them a lot.

#define DEFAULT_ACCELERATION          500 //3000    // X, Y, Z and E max acceleration in mm/s^2 for printing moves

#define DEFAULT_RETRACT_ACCELERATION  1000 //3000  // X, Y, Z and E max acceleration in mm/s^2 for retracts

¿Debajo de los drivers tienes colocados todos los jumpers? Si es así, con los drivers A4988 estarán configurados para 16 micropasos.

En el  archivo de Thingiverse están configurados para los DRV8825 con 32 micropasos, por eso solo tienes que cambiar en la fila de DEFAULT_AXIS_STEPS_PER_UNIT los valores a la mitad, excepto para el extrusor que me parece que es un GregWades. quiero recordar que estaba entorno a los 1800 micropasos, es decir que quedaría:

#define DEFAULT_AXIS_STEPS_PER_UNIT   {80.4, 80.4, 4000, 1800}

El extrusor lo podrás calibrar con precisión mas adelante.

Tu marco es muy grueso ¿de que material es?  Cuéntame cualquier problemilla,

Un saludo.

De: DavidAntRuiz [mailto:notifications@github.com]
Enviado el: viernes, 14 de octubre de 2016 9:40
Para: Mecan0/Code
CC: Manuel Palacios; Comment
Asunto: Re: [Mecan0/Code] Problema con Firmware (#4)

Gracias por responder Manuel.

De acuerdo, lo he encontrado, probaré cuando llegue a casa del trabajo.

Le comento una serie de problemas que me descolocan, por ejemplo, en sus configuraciones en el apartado:

#define DEFAULT_AXIS_STEPS_PER_UNIT

Yo he tenido que poner los valores #define DEFAULT_AXIS_STEPS_PER_UNIT {20,20,200,777} pero los he puesto de forma aleatoria... ¿Debe llevar una lógica? Pues siempre que veo el valor del eje Z por ejemplo es siempre muy elevado (4000, 8000...) sin embargo, si yo lo pongo con esos valores, el motor solo hace ruido y hace un pitido realmente desagradable, es decir, lo he puesto de manera aleatoria por que ha sido el único valor que ha "funcionado", y cuando digo "funcionado" quiero decir que ha sido la única vez que los ejes se han movido sin golpear con todo lo que había a su paso...

Creo que no estoy haciendo bien absolutamente nada relacionado con los motores... lo único que sé con seguridad que sí funciona son los finales de carrera.

Si me lo permite, adjunto un vídeo para que vea el funcionamiento actual de la impresora, esto ocurre cuando ha terminado de calentar y va a ponerse a imprimir.

Disculpe que se lo envíe todo en *.ZIP pero es que el formato de archivos permitidos para compartir es limitado

De todas formas, ya le digo que probaré en cuanto llegue con el que me acabo de descargar de Thingiverse y le comentaré el resultado adjuntando si lo requiere algún vídeo, imagen o archivo.

Saludos.

Video2016-10-14.zip <https://github.com/Mecan0/Code/files/528928/Video2016-10-14.zip>

—
You are receiving this because you commented.
Reply to this email directly, view it on GitHub <https://github.com/Mecan0/Code/issues/4#issuecomment-253731037> , or mute the thread <https://github.com/notifications/unsubscribe-auth/AEc83amUpaYPm8_mkSaPsm5I9ImqB3Cuks5qzzHmgaJpZM4KWAjD> .  <https://github.com/notifications/beacon/AEc83XLnVfEo-755413giGn9mtCWKuNnks5qzzHmgaJpZM4KWAjD.gif>

---
El software de antivirus Avast ha analizado este correo electrónico en busca de virus.
https://www.avast.com/antivirus

DavidAntRuiz, 2016-10-14:
mmm, de acuerdo, probaré todo lo que me comentas, debajo de los drivers no he puesto ningún jumper, los tengo, pero no los he puesto, no sabía que fueran necesarios, ¿Los pongo entonces, en todos los pines? ¿Qué influye exactamente?

El marco y la estructura en general es de metacrilato de 10mm, pues metacrilato de 5mm me parecía muy endeble y decidí usar el doble (1cm) para que quedase más resistente.

La verdad es que la impresora ha quedado bonita (al menos para mí), metacrilato negro brillante y las piezas rojas... creo que destaca mucho.

Sí, del extrusor no estoy pendiente, de hecho lo tengo subido para arriba para que no golpee el nozzle con la cama como hace lo que quiere y a una velocidad espasmosa... me daba miedo que se rompiera el extrusor.

Sí, efectivamente el extrusor es un GregWades.

El marlin que he cogido es el Marlin V1.1 - RC7 de github, será erroneo...así imposible que me funcionase jajaj

En definitiva, probaré con el suyo de Thingiverse y le comento.

De nuevo, gracias por su tiempo.

Saludos

Mecan0, 2016-10-14:
Cuando coloques los jumpers irá todo mejor :)

Si no los colocas, los drivers van a 1 paso por cada pulso que manda el software, como hemos dicho antes las impresoras trabajan normalmente con 16 o 32 micropasos.

Cada una de las 200 posiciones que tiene tu motor se divide en 16 o 32 micropasos, con lo cual aumenta mucho la resolución. El motor tendría teóricamente 3200 o 6400 posiciones posibles. Los pasos por mm (StepPerMM) que hemos configurado antes son para esas resoluciones.

La impresora te ha quedado muy guapa, yo la prefiero en aluminio, pero está muy chula.

Un saludo.

---
El software de antivirus Avast ha analizado este correo electrónico en busca de virus.
https://www.avast.com/antivirus

DavidAntRuiz, 2016-10-15:
Hola Manuel,

Tenías razón, con los jumpers ha mejorado muchíiiiisimo. Gracias.

Sigo teniendo un pequeño problema, cuando le he dado a imprimir un dado de 20x20mm, el eje Z no sube lo suficiente, es decir, el nozzle está tocando a la pieza constantemente y claro... lo que eso conlleva, una chapuza deformada....

¿Alguna sugerencia del porqué?

Saludos

Gracias

Mecan0, 2016-10-15:
Ese problema suele darse cuando estamos metiendo en el extrusor mas material de la cuenta y sobretodo con PLA.

La comprobación sencilla pasa por bajar el Flowrate en el programa de Host o en el Slic3r. Para solucionar el problema del todo debes calibrar el extrusor bien.

De todas formas es complicado eliminar ese problema por completo con el PLA.

---
El software de antivirus Avast ha analizado este correo electrónico en busca de virus.
https://www.avast.com/antivirus

DavidAntRuiz, 2016-10-15:
Efectivamente Manuel, pues aparentemente, todo correcto. Muchísimas gracias.

Ahora a calibrar bien la cama y que las capas me queden juntas entre sí pues me han quedado separadas en algunos sitios.

Saludos

DavidAntRuiz, 2016-10-18:
Manuel, todo correcto, le escribo para informarle que va de maravilla, ya funciona todo a la perfección.

Enhorabuena por su trabajo con la cama, se nivela "sola" prácticamente.

Saludos

Mecan0, 2016-10-20:
Gracias, me alegro de que te guste, un saludo.

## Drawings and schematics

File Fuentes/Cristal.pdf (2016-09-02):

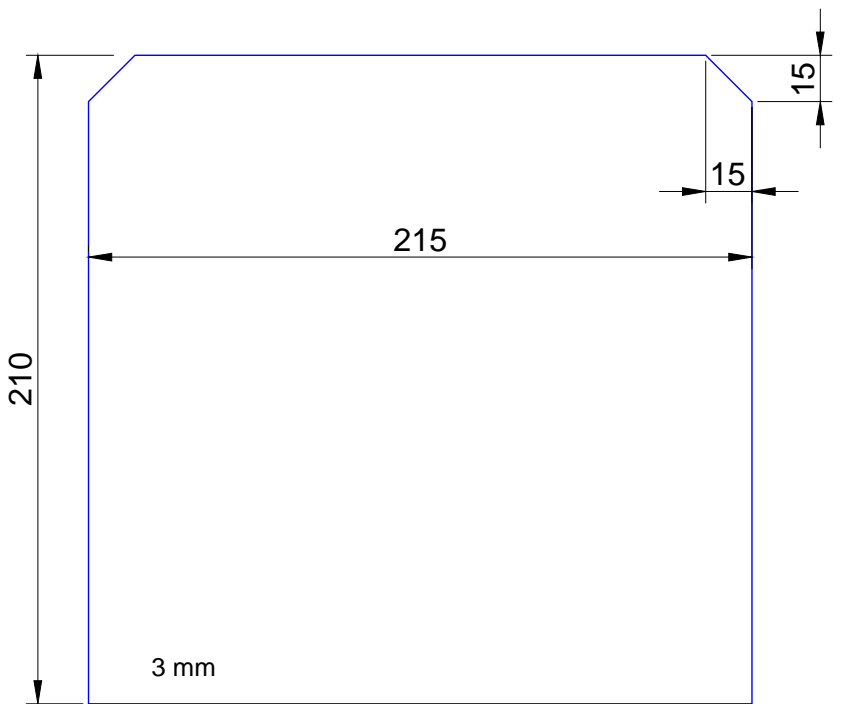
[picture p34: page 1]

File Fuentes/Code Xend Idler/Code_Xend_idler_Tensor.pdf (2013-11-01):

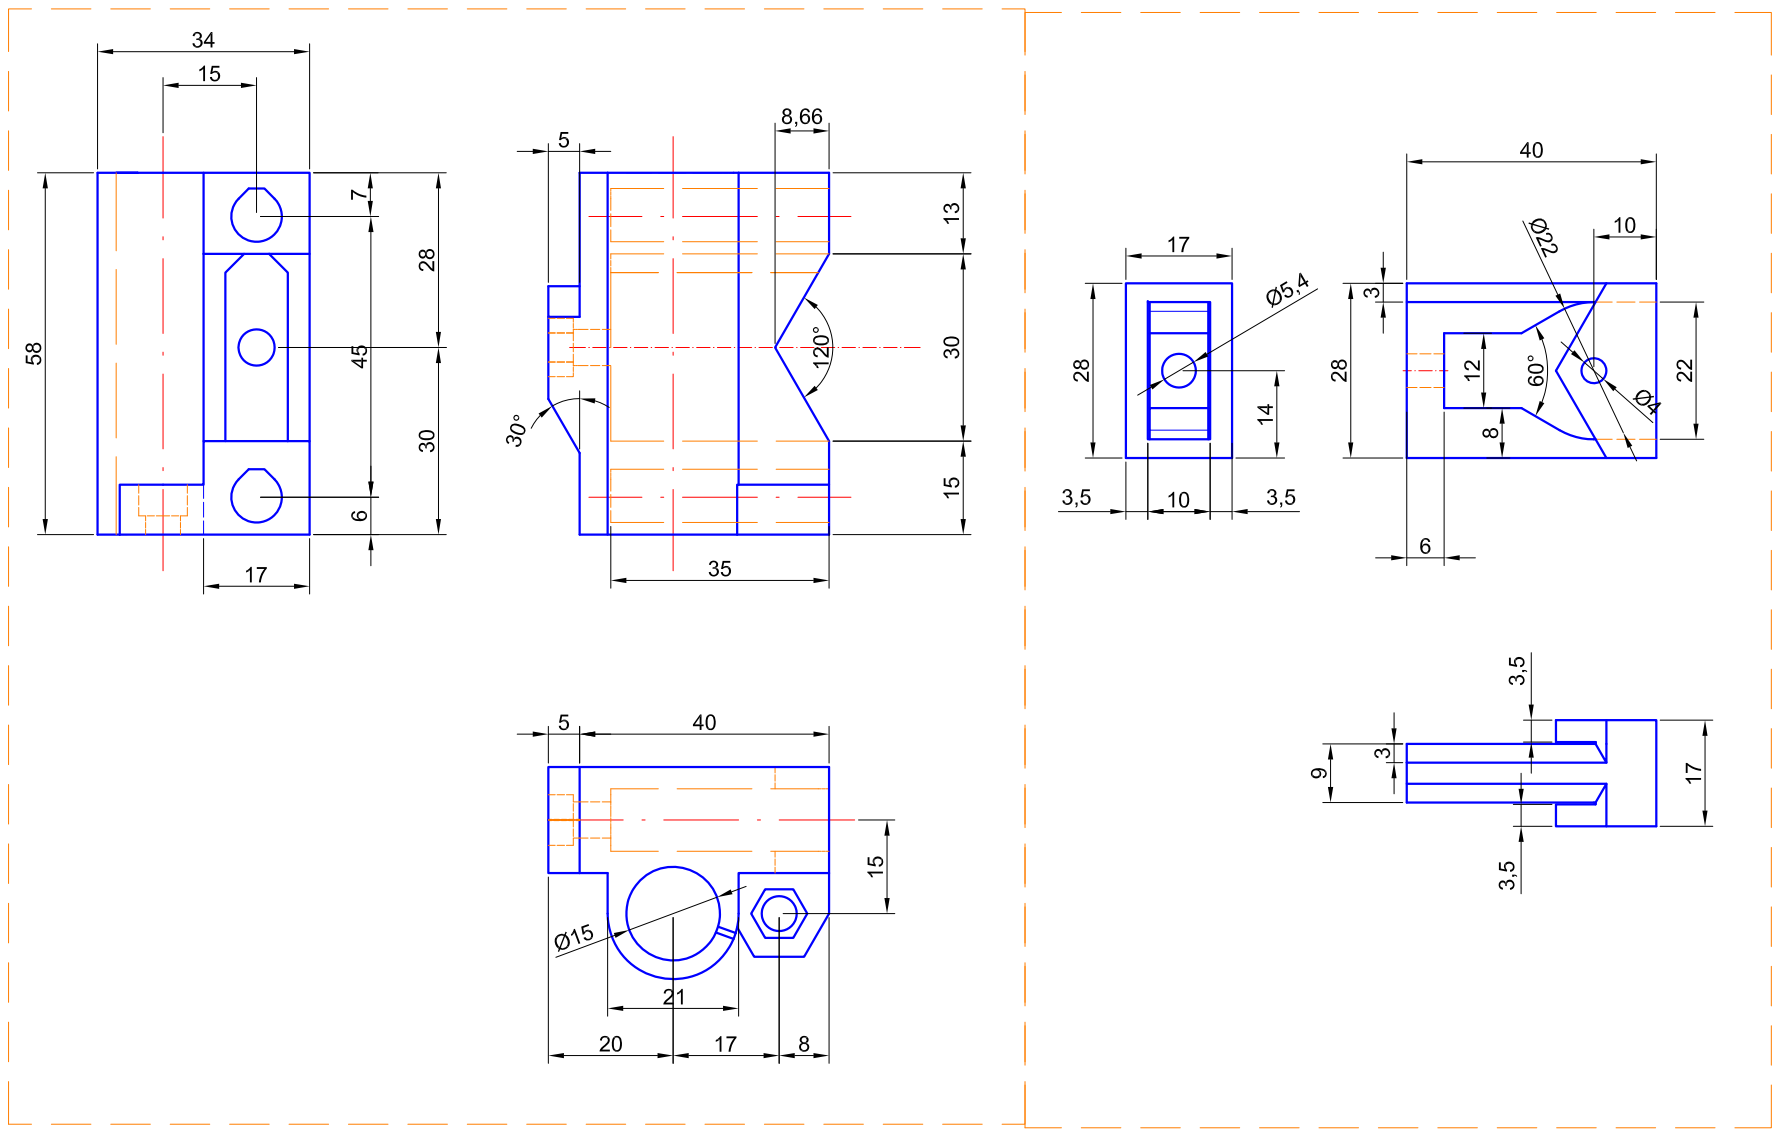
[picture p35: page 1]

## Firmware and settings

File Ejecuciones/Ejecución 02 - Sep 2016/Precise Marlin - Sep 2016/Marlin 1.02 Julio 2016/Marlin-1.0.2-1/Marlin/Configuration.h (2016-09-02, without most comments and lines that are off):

#define CONFIGURATION_H
#include "boards.h"
#define STRING_VERSION_CONFIG_H __DATE__ "29-Jun-2016" __TIME__ // build date and time
#define STRING_CONFIG_H_AUTHOR "(Manuel Palacios)" // Who made the changes.
#define SERIAL_PORT 0
#define BAUDRATE 250000
  #define MOTHERBOARD BOARD_RAMPS_13_EFB
#define CUSTOM_MENDEL_NAME "PowerCode"
#define EXTRUDERS 1
#define POWER_SUPPLY 1
#define TEMP_SENSOR_0 5
#define TEMP_SENSOR_1 0
#define TEMP_SENSOR_2 0
#define TEMP_SENSOR_BED 1
#define MAX_REDUNDANT_TEMP_SENSOR_DIFF 10
#define TEMP_RESIDENCY_TIME 10  // (seconds)
#define TEMP_HYSTERESIS 3       // (degC) range of +/- temperatures considered "close" to the target one
#define TEMP_WINDOW     1       // (degC) Window around target to start the residency timer x degC early.
#define HEATER_0_MINTEMP 5
#define HEATER_1_MINTEMP 5
#define HEATER_2_MINTEMP 5
#define BED_MINTEMP 5
#define HEATER_0_MAXTEMP 250
#define HEATER_1_MAXTEMP 275
#define HEATER_2_MAXTEMP 275
#define BED_MAXTEMP 150
#define PIDTEMP
#define BANG_MAX 255 // limits current to nozzle while in bang-bang mode; 255=full current
#define PID_MAX BANG_MAX // limits current to nozzle while PID is active (see PID_FUNCTIONAL_RANGE below); 255=full current
  #define PID_FUNCTIONAL_RANGE 10 // If the temperature difference between the target temperature and the actual temperature
  #define PID_INTEGRAL_DRIVE_MAX PID_MAX  //limit for the integral term
  #define K1 0.95 //smoothing factor within the PID
  #define PID_dT ((OVERSAMPLENR * 10.0)/(F_CPU / 64.0 / 256.0)) //sampling period of the temperature routine
    #define  DEFAULT_Kp 49 //41 // 45.30
    #define  DEFAULT_Ki 7 //5.50 // 6.50
    #define  DEFAULT_Kd 83 //75 // 80.30
#define MAX_BED_POWER 255 // limits duty cycle to bed; 255=full current
#define PREVENT_DANGEROUS_EXTRUDE
#define PREVENT_LENGTHY_EXTRUDE
#define EXTRUDE_MINTEMP 170
#define EXTRUDE_MAXLENGTH (X_MAX_LENGTH+Y_MAX_LENGTH) //prevent extrusion of very large distances.
#define ENDSTOPPULLUPS // Comment this out (using // at the start of the line) to disable the endstop pullup resistors
  #define ENDSTOPPULLUP_XMAX
  #define ENDSTOPPULLUP_YMAX
  #define ENDSTOPPULLUP_ZMAX
  #define ENDSTOPPULLUP_XMIN
  #define ENDSTOPPULLUP_YMIN
  #define ENDSTOPPULLUP_ZMIN
const bool X_MIN_ENDSTOP_INVERTING = true; // set to true to invert the logic of the endstop.
const bool Y_MIN_ENDSTOP_INVERTING = true; // set to true to invert the logic of the endstop.
const bool Z_MIN_ENDSTOP_INVERTING = true; // set to true to invert the logic of the endstop.
const bool X_MAX_ENDSTOP_INVERTING = true; // set to true to invert the logic of the endstop.
const bool Y_MAX_ENDSTOP_INVERTING = true; // set to true to invert the logic of the endstop.
const bool Z_MAX_ENDSTOP_INVERTING = true; // set to true to invert the logic of the endstop.
#if defined(COREXY) && !defined(DISABLE_MAX_ENDSTOPS)
  #define DISABLE_MAX_ENDSTOPS
#endif
#define X_ENABLE_ON 0
#define Y_ENABLE_ON 0
#define Z_ENABLE_ON 0
#define E_ENABLE_ON 0 // For all extruders
#define DISABLE_X false
#define DISABLE_Y false
#define DISABLE_Z false
#define DISABLE_E false // For all extruders
#define DISABLE_INACTIVE_EXTRUDER true //disable only inactive extruders and keep active extruder enabled
#define INVERT_X_DIR true    // for Mendel set to false, for Orca set to true
#define INVERT_Y_DIR false    // for Mendel set to true, for Orca set to false
#define INVERT_Z_DIR true     // for Mendel set to false, for Orca set to true
#define INVERT_E0_DIR true   // Titan //for direct drive extruder v9 set to true, for geared extruder set to false
#define INVERT_E1_DIR false    // for direct drive extruder v9 set to true, for geared extruder set to false
#define INVERT_E2_DIR false   // for direct drive extruder v9 set to true, for geared extruder set to false
#define X_HOME_DIR -1
#define Y_HOME_DIR -1
#define Z_HOME_DIR -1
#define min_software_endstops true // If true, axis won't move to coordinates less than HOME_POS.
#define max_software_endstops true  // If true, axis won't move to coordinates greater than the defined lengths below.
#define X_MAX_POS 195
#define X_MIN_POS 0
#define Y_MAX_POS 190
#define Y_MIN_POS 0
#define Z_MAX_POS 180
#define Z_MIN_POS 0
#define X_MAX_LENGTH (X_MAX_POS - X_MIN_POS)
#define Y_MAX_LENGTH (Y_MAX_POS - Y_MIN_POS)
#define Z_MAX_LENGTH (Z_MAX_POS - Z_MIN_POS)
#define Z_PROBE_REPEATABILITY_TEST  // If not commented out, Z-Probe Repeatability test will be included if Auto Bed Leveling is Enabled.
#define MANUAL_X_HOME_POS 0
#define MANUAL_Y_HOME_POS 0
#define MANUAL_Z_HOME_POS 0
#define NUM_AXIS 4 // The axis order in all axis related arrays is X, Y, Z, E
#define HOMING_FEEDRATE {35*60, 35*60, 2,5*60, 0} //{50*60, 50*60, 4*60, 0}  // set the homing speeds (mm/min)
#define DEFAULT_AXIS_STEPS_PER_UNIT   {160.9, 160.9, 8000, 912}  // Driver DRV8825 con 32 micropasos
#define DEFAULT_MAX_FEEDRATE          {200, 200, 2.5, 15} // {500, 500, 5, 25}  // (mm/sec)
#define DEFAULT_MAX_ACCELERATION      {500,500,50,1000} //{9000,9000,100,10000}    // X, Y, Z, E maximum start speed for accelerated moves. E default values are good for Skeinforge 40+, for older versions raise them a lot.
#define DEFAULT_ACCELERATION          500 //3000    // X, Y, Z and E max acceleration in mm/s^2 for printing moves
#define DEFAULT_RETRACT_ACCELERATION  1000 //3000  // X, Y, Z and E max acceleration in mm/s^2 for retracts
#define DEFAULT_XYJERK                10.0  // 20 // (mm/sec)
#define DEFAULT_ZJERK                 0.4     // (mm/sec)
#define DEFAULT_EJERK                 5.0    // (mm/sec)
#define CUSTOM_M_CODES
  #define CUSTOM_M_CODE_SET_Z_PROBE_OFFSET 851
  #define Z_PROBE_OFFSET_RANGE_MIN -15
  #define Z_PROBE_OFFSET_RANGE_MAX -5
#define PLA_PREHEAT_HOTEND_TEMP 180
#define PLA_PREHEAT_HPB_TEMP 70
#define PLA_PREHEAT_FAN_SPEED 255   // Insert Value between 0 and 255
#define ABS_PREHEAT_HOTEND_TEMP 240
#define ABS_PREHEAT_HPB_TEMP 100
#define ABS_PREHEAT_FAN_SPEED 255   // Insert Value between 0 and 255
#define REPRAP_DISCOUNT_SMART_CONTROLLER
 #define ULTIPANEL
 #define NEWPANEL
  #define SDSUPPORT
  #define ULTRA_LCD
    #define LCD_WIDTH 20
    #define LCD_HEIGHT 4
#define SOFT_PWM_SCALE 0
#define FILAMENT_SENSOR_EXTRUDER_NUM	0  //The number of the extruder that has the filament sensor (0,1,2)
#define MEASUREMENT_DELAY_CM			14  //measurement delay in cm.  This is the distance from filament sensor to middle of barrel
#define DEFAULT_NOMINAL_FILAMENT_DIA  3.0  //Enter the diameter (in mm) of the filament generally used (3.0 mm or 1.75 mm) - this is then used in the slicer software.  Used for sensor reading validation
#define MEASURED_UPPER_LIMIT          3.30  //upper limit factor used for sensor reading validation in mm
#define MEASURED_LOWER_LIMIT          1.90  //lower limit factor for sensor reading validation in mm
#define MAX_MEASUREMENT_DELAY			20  //delay buffer size in bytes (1 byte = 1cm)- limits maximum measurement delay allowable (must be larger than MEASUREMENT_DELAY_CM  and lower number saves RAM)
#define DEFAULT_MEASURED_FILAMENT_DIA  DEFAULT_NOMINAL_FILAMENT_DIA  //set measured to nominal initially
#include "Configuration_adv.h"
#include "thermistortables.h"

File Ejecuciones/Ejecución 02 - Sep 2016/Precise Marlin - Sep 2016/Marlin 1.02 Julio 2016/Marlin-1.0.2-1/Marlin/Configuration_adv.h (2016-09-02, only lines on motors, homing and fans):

#define CONTROLLERFAN_PIN -1 //Pin used for the fan to cool controller (-1 to disable)
#define EXTRUDER_0_AUTO_FAN_PIN   -1
#define EXTRUDER_1_AUTO_FAN_PIN   -1
#define EXTRUDER_2_AUTO_FAN_PIN   -1
#define ENDSTOPS_ONLY_FOR_HOMING // If defined the endstops will only be used for homing
#define X_HOME_RETRACT_MM 5
#define Y_HOME_RETRACT_MM 5
#define Z_HOME_RETRACT_MM 1
#define MICROSTEP1 LOW,LOW
#define MICROSTEP2 HIGH,LOW
#define MICROSTEP4 LOW,HIGH
#define MICROSTEP8 HIGH,HIGH
#define MICROSTEP16 HIGH,HIGH
#define MICROSTEP_MODES {16,16,16,16,16} // [1,2,4,8,16]
#define DIGIPOT_MOTOR_CURRENT {135,135,135,135,135} // Values 0-255 (RAMBO 135 = ~0.75A, 185 = ~1A)
#define DIGIPOT_I2C_MOTOR_CURRENTS {1.0, 1.0, 1.0, 1.0, 1.0, 1.0, 1.0, 1.0}

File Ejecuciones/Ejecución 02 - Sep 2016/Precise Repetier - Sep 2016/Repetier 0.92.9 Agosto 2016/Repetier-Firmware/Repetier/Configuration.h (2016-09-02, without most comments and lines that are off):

#define CONFIGURATION_H
#define NUM_EXTRUDER 1
#define MOTHERBOARD 33
#include "pins.h"
#undef FAN_BOARD_PIN
#define FAN_BOARD_PIN -1
#define BOARD_FAN_SPEED 255
#define FAN_THERMO_PIN -1
#define FAN_THERMO_MIN_PWM 128
#define FAN_THERMO_MAX_PWM 255
#define FAN_THERMO_MIN_TEMP 45
#define FAN_THERMO_MAX_TEMP 60
#define FAN_THERMO_THERMISTOR_PIN -1
#define FAN_THERMO_THERMISTOR_TYPE 1
#define BLUETOOTH_SERIAL  -1
#define BLUETOOTH_BAUD  115200
#define MIXING_EXTRUDER 0
#define DRIVE_SYSTEM 0
#define XAXIS_STEPS_PER_MM 160.9
#define YAXIS_STEPS_PER_MM 160.9
#define ZAXIS_STEPS_PER_MM 8000
#define EXTRUDER_FAN_COOL_TEMP 50
#define PDM_FOR_EXTRUDER 0
#define PDM_FOR_COOLER 0
#define DECOUPLING_TEST_MAX_HOLD_VARIANCE 20
#define DECOUPLING_TEST_MIN_TEMP_RISE 1
#define KILL_IF_SENSOR_DEFECT 0
#define RETRACT_ON_PAUSE 2
#define PAUSE_START_COMMANDS ""
#define PAUSE_END_COMMANDS ""
#define SHARED_EXTRUDER_HEATER 0
#define EXT0_X_OFFSET 0
#define EXT0_Y_OFFSET 0
#define EXT0_Z_OFFSET 0
#define EXT0_STEPS_PER_MM 912
#define EXT0_TEMPSENSOR_TYPE 8
#define EXT0_TEMPSENSOR_PIN TEMP_0_PIN
#define EXT0_HEATER_PIN HEATER_0_PIN
#define EXT0_STEP_PIN ORIG_E0_STEP_PIN
#define EXT0_DIR_PIN ORIG_E0_DIR_PIN
#define EXT0_INVERSE 1
#define EXT0_ENABLE_PIN ORIG_E0_ENABLE_PIN
#define EXT0_ENABLE_ON 0
#define EXT0_MIRROR_STEPPER 0
#define EXT0_STEP2_PIN ORIG_E0_STEP_PIN
#define EXT0_DIR2_PIN ORIG_E0_DIR_PIN
#define EXT0_INVERSE2 0
#define EXT0_ENABLE2_PIN ORIG_E0_ENABLE_PIN
#define EXT0_MAX_FEEDRATE 15
#define EXT0_MAX_START_FEEDRATE 3
#define EXT0_MAX_ACCELERATION 1000
#define EXT0_HEAT_MANAGER 1
#define EXT0_WATCHPERIOD 1
#define EXT0_PID_INTEGRAL_DRIVE_MAX 230
#define EXT0_PID_INTEGRAL_DRIVE_MIN 40
#define EXT0_PID_PGAIN_OR_DEAD_TIME 28
#define EXT0_PID_I 4.5
#define EXT0_PID_D 43
#define EXT0_PID_MAX 255
#define EXT0_ADVANCE_K 0
#define EXT0_ADVANCE_L 0
#define EXT0_ADVANCE_BACKLASH_STEPS 0
#define EXT0_WAIT_RETRACT_TEMP 150
#define EXT0_WAIT_RETRACT_UNITS 0
#define EXT0_SELECT_COMMANDS ""
#define EXT0_DESELECT_COMMANDS ""
#define EXT0_EXTRUDER_COOLER_PIN -1
#define EXT0_EXTRUDER_COOLER_SPEED 255
#define EXT0_DECOUPLE_TEST_PERIOD 12000
#define EXT0_JAM_PIN -1
#define EXT0_JAM_PULLUP 0
#define FEATURE_RETRACTION 1
#define AUTORETRACT_ENABLED 0
#define RETRACTION_LENGTH 3
#define RETRACTION_LONG_LENGTH 13
#define RETRACTION_SPEED 40
#define RETRACTION_Z_LIFT 0
#define RETRACTION_UNDO_EXTRA_LENGTH 0
#define RETRACTION_UNDO_EXTRA_LONG_LENGTH 0
#define RETRACTION_UNDO_SPEED 20
#define FILAMENTCHANGE_X_POS 0
#define FILAMENTCHANGE_Y_POS 0
#define FILAMENTCHANGE_Z_ADD  2
#define FILAMENTCHANGE_REHOME 1
#define FILAMENTCHANGE_SHORTRETRACT 5
#define FILAMENTCHANGE_LONGRETRACT 50
#define JAM_STEPS 220
#define JAM_SLOWDOWN_STEPS 320
#define JAM_SLOWDOWN_TO 70
#define JAM_ERROR_STEPS 500
#define JAM_MIN_STEPS 10
#define JAM_ACTION 1
#define RETRACT_DURING_HEATUP true
#define PID_CONTROL_RANGE 20
#define SKIP_M109_IF_WITHIN 2
#define SCALE_PID_TO_MAX 0
#define TEMP_HYSTERESIS 0
#define EXTRUDE_MAXLENGTH 160
#define NUM_TEMPS_USERTHERMISTOR0 0
#define USER_THERMISTORTABLE0 {}
#define NUM_TEMPS_USERTHERMISTOR1 0
#define USER_THERMISTORTABLE1 {}
#define NUM_TEMPS_USERTHERMISTOR2 0
#define USER_THERMISTORTABLE2 {}
#define GENERIC_THERM_VREF 5
#define GENERIC_THERM_NUM_ENTRIES 33
#define HEATER_PWM_SPEED 0
#define HAVE_HEATED_BED 1
#define HEATED_BED_MAX_TEMP 110
#define SKIP_M190_IF_WITHIN 3
#define HEATED_BED_SENSOR_TYPE 1
#define HEATED_BED_SENSOR_PIN TEMP_1_PIN
#define HEATED_BED_HEATER_PIN HEATER_1_PIN
#define HEATED_BED_SET_INTERVAL 5000
#define HEATED_BED_HEAT_MANAGER 0
#define HEATED_BED_PID_INTEGRAL_DRIVE_MAX 255
#define HEATED_BED_PID_INTEGRAL_DRIVE_MIN 80
#define HEATED_BED_PID_PGAIN_OR_DEAD_TIME   196
#define HEATED_BED_PID_IGAIN   33
#define HEATED_BED_PID_DGAIN 290
#define HEATED_BED_PID_MAX 255
#define HEATED_BED_DECOUPLE_TEST_PERIOD 300000
#define MIN_EXTRUDER_TEMP 150
#define MAXTEMP 250
#define MIN_DEFECT_TEMPERATURE -10
#define MAX_DEFECT_TEMPERATURE 290
#define SUPPORT_LASER 1
#define LASER_PIN -1
#define LASER_ON_HIGH 1
#define SUPPORT_CNC 1
#define CNC_WAIT_ON_ENABLE 300
#define CNC_WAIT_ON_DISABLE 0
#define CNC_ENABLE_PIN -1
#define CNC_ENABLE_WITH 1
#define CNC_DIRECTION_PIN -1
#define CNC_DIRECTION_CW 1
#define DEFAULT_PRINTER_MODE 0
#define ENDSTOP_PULLUP_X_MIN true
#define ENDSTOP_X_MIN_INVERTING true
#define MIN_HARDWARE_ENDSTOP_X true
#define ENDSTOP_PULLUP_Y_MIN true
#define ENDSTOP_Y_MIN_INVERTING true
#define MIN_HARDWARE_ENDSTOP_Y true
#define ENDSTOP_PULLUP_Z_MIN true
#define ENDSTOP_Z_MIN_INVERTING true
#define MIN_HARDWARE_ENDSTOP_Z true
#define ENDSTOP_PULLUP_X_MAX true
#define ENDSTOP_X_MAX_INVERTING false
#define MAX_HARDWARE_ENDSTOP_X false
#define ENDSTOP_PULLUP_Y_MAX true
#define ENDSTOP_Y_MAX_INVERTING false
#define MAX_HARDWARE_ENDSTOP_Y false
#define ENDSTOP_PULLUP_Z_MAX true
#define ENDSTOP_Z_MAX_INVERTING false
#define MAX_HARDWARE_ENDSTOP_Z false
#define max_software_endstop_r true
#define min_software_endstop_x false
#define min_software_endstop_y false
#define min_software_endstop_z false
#define max_software_endstop_x true
#define max_software_endstop_y true
#define max_software_endstop_z true
#define ENDSTOP_X_BACK_MOVE 5
#define ENDSTOP_Y_BACK_MOVE 5
#define ENDSTOP_Z_BACK_MOVE 2
#define ENDSTOP_X_RETEST_REDUCTION_FACTOR 3
#define ENDSTOP_Y_RETEST_REDUCTION_FACTOR 3
#define ENDSTOP_Z_RETEST_REDUCTION_FACTOR 3
#define ENDSTOP_X_BACK_ON_HOME 1
#define ENDSTOP_Y_BACK_ON_HOME 1
#define ENDSTOP_Z_BACK_ON_HOME 0
#define ALWAYS_CHECK_ENDSTOPS 1
#define X_ENABLE_ON 0
#define Y_ENABLE_ON 0
#define Z_ENABLE_ON 0
#define DISABLE_X 0
#define DISABLE_Y 0
#define DISABLE_Z 1
#define DISABLE_E 0
#define INVERT_X_DIR 1
#define INVERT_Y_DIR 0
#define INVERT_Z_DIR 1
#define X_HOME_DIR -1
#define Y_HOME_DIR -1
#define Z_HOME_DIR -1
#define X_MAX_LENGTH 190
#define Y_MAX_LENGTH 190
#define Z_MAX_LENGTH 190
#define X_MIN_POS 0
#define Y_MIN_POS 0
#define Z_MIN_POS 0
#define DISTORTION_CORRECTION 0
#define DISTORTION_CORRECTION_POINTS 5
#define DISTORTION_CORRECTION_R 100
#define DISTORTION_PERMANENT 1
#define DISTORTION_UPDATE_FREQUENCY 15
#define DISTORTION_START_DEGRADE 0.5
#define DISTORTION_END_HEIGHT 1
#define DISTORTION_EXTRAPOLATE_CORNERS 0
#define DISTORTION_XMIN 10
#define DISTORTION_YMIN 10
#define DISTORTION_XMAX 190
#define DISTORTION_YMAX 190
#define FEATURE_BABYSTEPPING 1
#define BABYSTEP_MULTIPLICATOR 1
#define DELTA_SEGMENTS_PER_SECOND_PRINT 180 // Move accurate setting for print moves
#define DELTA_SEGMENTS_PER_SECOND_MOVE 70 // Less accurate setting for other moves
#define EXACT_DELTA_MOVES 1
#define DELTA_HOME_ON_POWER 0
#define DELTASEGMENTS_PER_PRINTLINE 24
#define STEPPER_INACTIVE_TIME 360L
#define MAX_INACTIVE_TIME 0L
#define MAX_FEEDRATE_X 200
#define MAX_FEEDRATE_Y 200
#define MAX_FEEDRATE_Z 2.5
#define HOMING_FEEDRATE_X 40
#define HOMING_FEEDRATE_Y 40
#define HOMING_FEEDRATE_Z 2.5
#define HOMING_ORDER HOME_ORDER_XYZ
#define ZHOME_MIN_TEMPERATURE 0
#define ZHOME_HEAT_ALL 1
#define ZHOME_HEAT_HEIGHT 20
#define ZHOME_X_POS 999999
#define ZHOME_Y_POS 999999
#define ENABLE_BACKLASH_COMPENSATION 0
#define X_BACKLASH 0
#define Y_BACKLASH 0
#define Z_BACKLASH 0
#define RAMP_ACCELERATION 1
#define STEPPER_HIGH_DELAY 0
#define DIRECTION_DELAY 0
#define STEP_DOUBLER_FREQUENCY 12000
#define ALLOW_QUADSTEPPING 1
#define DOUBLE_STEP_DELAY 0 // time in microseconds
#define MAX_ACCELERATION_UNITS_PER_SQ_SECOND_X 500
#define MAX_ACCELERATION_UNITS_PER_SQ_SECOND_Y 500
#define MAX_ACCELERATION_UNITS_PER_SQ_SECOND_Z 50
#define MAX_TRAVEL_ACCELERATION_UNITS_PER_SQ_SECOND_X 500
#define MAX_TRAVEL_ACCELERATION_UNITS_PER_SQ_SECOND_Y 500
#define MAX_TRAVEL_ACCELERATION_UNITS_PER_SQ_SECOND_Z 50
#define INTERPOLATE_ACCELERATION_WITH_Z 0
#define ACCELERATION_FACTOR_TOP 100
#define MAX_JERK 10
#define MAX_ZJERK 0.3
#define PRINTLINE_CACHE_SIZE 16
#define MOVE_CACHE_LOW 10
#define LOW_TICKS_PER_MOVE 250000
#define EXTRUDER_SWITCH_XY_SPEED 100
#define DUAL_X_AXIS 0
#define FEATURE_TWO_XSTEPPER 0
#define X2_STEP_PIN   ORIG_E1_STEP_PIN
#define X2_DIR_PIN    ORIG_E1_DIR_PIN
#define X2_ENABLE_PIN ORIG_E1_ENABLE_PIN
#define FEATURE_TWO_YSTEPPER 0
#define Y2_STEP_PIN   ORIG_E1_STEP_PIN
#define Y2_DIR_PIN    ORIG_E1_DIR_PIN
#define Y2_ENABLE_PIN ORIG_E1_ENABLE_PIN
#define FEATURE_TWO_ZSTEPPER 0
#define Z2_STEP_PIN   ORIG_E1_STEP_PIN
#define Z2_DIR_PIN    ORIG_E1_DIR_PIN
#define Z2_ENABLE_PIN ORIG_E1_ENABLE_PIN
#define FEATURE_THREE_ZSTEPPER 0
#define Z3_STEP_PIN   ORIG_E2_STEP_PIN
#define Z3_DIR_PIN    ORIG_E2_DIR_PIN
#define Z3_ENABLE_PIN ORIG_E2_ENABLE_PIN
#define FEATURE_DITTO_PRINTING 0
#define USE_ADVANCE 0
#define ENABLE_QUADRATIC_ADVANCE 0
#define BAUDRATE 250000
#define ENABLE_POWER_ON_STARTUP 1
#define POWER_INVERTING 0
#define KILL_METHOD 1
#define ACK_WITH_LINENUMBER 1
#define WAITING_IDENTIFIER "wait"
#define ECHO_ON_EXECUTE 1
#define EEPROM_MODE 2
#undef PS_ON_PIN
#define PS_ON_PIN ORIG_PS_ON_PIN
#define JSON_OUTPUT 0
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

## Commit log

2013-10-07 Revisión 01
    [Aluminio Power Code.dxf, ArandExtru.stl, CarcasaRamps.stl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]
2013-11-01 No van bien
    [Code_EndStopHolder Hall Bueno.stl, Code_EndStopHolder_experimental.stl]
2013-11-01 Mas profundidad para el rodamiento
    [Code_Pulley_623 (x4).stl]
2013-11-01 Mas apertura para alojar la polea
    [Code_Yidler_623.stl]
2013-11-01 Fuentes dxf
    [Code Clip RAMPS.dxf, CodeEndStopHolder.dxf]
2013-11-01 Añadidas fotos de montaje
2013-11-01 Nuevo soporte para finales de carrera
    [Code_EndStop (x2).stl]
2013-11-01 Unificados los soportes en una sola pieza
    [Code_Clip_ RAMPS.stl]
2013-11-01 Endstop holder
    [Code_EndStop (x2).stl]
2013-11-01 El casquillo se fija con una brida, desliza mejor.
    [Code_Xcarriage - A_Igus_Nueva Versión.stl]
2013-11-01 Alojamientos Igus pasan de 16 a 16.2
    Los taladros de las varillas pasan de 8.1 a 8.15.
    Tuerca de M3 para el prisionero pasa a entrecaras 5.8.
    [Code_Xend_Idler_A_Igus.stl]
2013-11-01 Mas uña y menos presión
    [Code_Clip_ RAMPS.stl, Code_Clip_RAMPS.stl]
2013-11-02 Movidos a carpeta Logo
    [LogoCode.stl, LogoCodeNegativo.stl]
2013-11-02 Añadida fuente en dxf
    [LogoPowerCode.dxf]
2013-11-03 Cambiados de carpeta
    [Aluminio Power Code.dxf, CarcasaRamps.stl, Code_EndStopHolder Hall.stl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]
2013-11-03 Nueva versión para tensor con tornillo M6
    [Code_Xend_Idler_A_Igus_M6.stl, Code_Xend_Idler_B_623_M6.stl]
2013-11-03 Esquina redondeada
    Alojamiento Igus 16,2
    [Code_Xend_Motor_Igus.stl]
2013-11-16 1 mm de clareo
    [LogoCodeNegativo.stl]
2013-12-01 Añadidas carpetas para diferentes ejecuciones
    [Code_Plato_1.stl, Code_Plato_2.stl]
2013-12-01 Mas juego para las letras del negativo
    [LogoPowerCode.dxf]
2013-12-04 Clip para equipar la PowerCode con la SAV-MK1
    [Code Clip SAVMK1.dxf, Code_Clip_SAV-MK1.stl, Code_Clip_SAV-MK1_arriba.stl]
2013-12-08 Firmware para Arduino 1.05 actualizado y robusto
    [Configuration.h, Configuration_adv.h]
2013-12-08 LCD de RRD, atornillar sobre el motor Z.
    Preferiblemente el motor Z que está en el lado de la electronica.
    La pcb de rrd puede cambiar, hay varios modelos.
    [Code_soporte_LCD_RRD.stl, RuletaLCD.stl]
2013-12-08 Quitado Ymin
    [Configuration.h]
2014-01-01 Movidos a obsoletos
    [Code_Xcarriage_A.stl, Code_Xend_Idler_A.stl]
2014-01-01 Alojamiento para LM8UU 15.2
    Alojamiento para varillas 8.2
    [Code_Xend_Motor.stl]
2014-01-01 Cambiado para tensor M6
    Alojamiento para LM8uu 15.2
    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
    [Code_Xend_Idler_A_M6.stl]
2014-01-01 Nuevo Xcarriage
    [Nuevo_Code_Xcarriage - A.stl]
2014-01-01 Movidos de carpeta
    [Code_Xend_Idler_B_623_M5.stl, Code_Xend_Idler_B_623_M6.stl]
2014-02-02 Borrado por repetido
    [Code_Xend-motor.stl]
2014-02-02 Incluye soporte para tornillo de regulación de Z
    [Code_Xend_Motor_Tornillo.stl]
2014-02-02 Archivo añadido
    Añadida la primera revisión de los archivos en formato OpenSCAD
    (*.scad).
    [Code_Clip_RAMPS.scad, Code_Config.scad, Code_Diagonal.scad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]
2014-02-13 Fix
    Arreglado la diferencia de 1mm en el tope central.
    [Code_Clip_RAMPS.scad]
2014-02-13 Fix Taladros
    Arreglada la posición de los taladros de los bloques X y Y.
    [Code_Diagonal.scad]
2014-02-13 Renombrado
    Rename Code_Diagonal.scad to Code_Diagonal (x2).scad
    [Code_Diagonal (x2).scad]
2014-02-13 Fix Medidas
    Se ha redimensionado la pieza porque le faltaba 0,5 mm de largo y se ha
    corregido la posición del redondeo interior para la varilla.
    [Code_Ycorner.scad]
2014-02-13 Fix Chaflanes
    Se ha corregido el ángulo de los chaflanes interiores y se ha añadido un
    chaflán faltante en la parte inferior junto al redondeo.
    [Code_Yidler_623.scad]
2014-02-13 Fix Posición
    Arreglada la posición del tornillo de sujeción al marco.
    [Code_Zbotton.scad]
2014-02-18 Cambiados los pasos x mm
    [Configuration.h]
2014-02-18 Cubo de calibración sencillo
    Es un cubo de 40x40x10, una vez impreso debe entrar una tuerca M10 de
    16.75 mm entrecaras y una moneda de un euro en los laterales.
    [CuboCalibracion_01.stl]
2014-02-19 Archivo añadido
    [Code_Xcarriage_A (Nuevo).scad]
2014-03-16 Añadidos dos parámetros
    Se han añadido dos parámetros faltantes de los cojinetes lineales (dCoLi
    y dVaLi).
    [Code_Config.scad]
2014-03-29 Sustituido por la versión con tornillo
    [Code_Xend_Motor.stl, Code_Xend_Motor_Tornillo.stl]
2014-05-21 Eliminados por limpieza
    [Code_EndStopHolder Hall.stl, Code_Pulley_623 (x4) diam 10.2.stl, Code_Xcarriage - A_Igus.stl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]
2014-05-21 Aspirantes a definitivos
    X-ends abiertos en el alojamiento de las varillas lisas para un montaje
    mas fácil.
    [Code_Xend_Idler_A_M6_Open.stl, Code_Xend_Motor_Open.stl]
2014-05-23 Añadida pestaña para fijar posición
    [Code_Xend_Idler_A_M6_Open.stl]
2014-07-10 Nuevo Xcarriage Unibody
    [Code_XCarriage_Unibody_Igus.stl]
2015-04-19 Igus antiguo de 16 mm de diam.
    [Code_Xcarriage - A_Igus_Nueva Versión.stl, Code_Xend_Idler_A_M6_Igus.stl, Code_Xend_Motor_Igus.stl]
2015-04-19 Movidos a otra carpeta
    [Code_Clip_RAMPS.stl, Code_LevelExtruder.stl, Code_XCarriage_Unibody_Igus.stl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]
2015-04-19 Nuevo, mas robusto!
    [Code_Xcarriage_A.stl]
2015-04-19 Movido a otra carpeta
    [CuboCalibracion_01.stl]
2015-04-19 Para rodamiento 686, el eje es un tornillo de 6 mm.
    [Code_Xend_Idler_B_686_M6 M6.stl]
2016-03-05 Revisión con muchas mejoras
    Cambiada polea por rodamiento 685ZZ con eje M5 y arandelas estandar y de
    vuelo M5.
    685ZZ: Diam ext 11 m, anchura 5mm
    [Code_Clip-ElectronicaRampsBQ.stl, Code_EndStop (x2).stl, Code_FinalCarreraPCB_XY.stl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]
2016-09-02 Ejecución Precise
    [01 Diagonal.stl, 02 Ycorner.stl, 03 Ybelt_A.stl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]

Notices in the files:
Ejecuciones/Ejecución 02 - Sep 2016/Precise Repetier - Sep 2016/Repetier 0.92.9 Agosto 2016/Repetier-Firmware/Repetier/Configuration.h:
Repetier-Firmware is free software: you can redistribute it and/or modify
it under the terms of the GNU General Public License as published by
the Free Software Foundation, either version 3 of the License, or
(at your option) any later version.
